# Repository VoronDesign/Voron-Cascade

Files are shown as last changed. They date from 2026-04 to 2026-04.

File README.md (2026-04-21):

# Voron Cascade
**[CLICK HERE TO DOWNLOAD](https://voron.zip/done/VC.zip)**

Image of Voron Cascade

The official release of the Voron Cascade desktop CNC milling machine.  You can find the BOM in the CAD directory or located at the [Voron Design](http://vorondesign.com/voron_cascade) website.

Voron Logo

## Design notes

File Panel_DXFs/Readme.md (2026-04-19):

\[sp-o\] for an opaque panel, structural / safety  
\[sp-c\] for a clear panel, structural / safety  
\[ep-o\] for an opaque panel used for an enclosure, non-structural  
\[ep-c\] for a clear panel used for an enclosure, non-structural

Frame bottom and gantry opaque panels should be 3mm (1/8") aluminum or steel.

Working enclosure clear panels should be 5mm (3/16") polycarbonate.

Frame or printed enclosure opaque panels should be 3mm (1/8") ABS.

Frame or printed enclosure clear panels should be 3mm (1/8") acrylic, preferably tinted ("smoked").

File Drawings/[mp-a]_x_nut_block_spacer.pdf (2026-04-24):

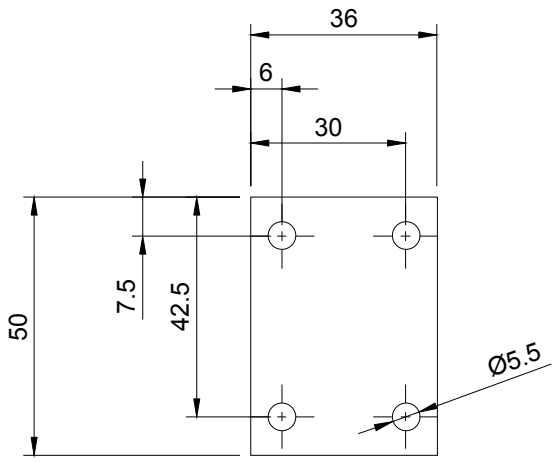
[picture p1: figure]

8.6

[mp-a]_x_nut_block_spacer

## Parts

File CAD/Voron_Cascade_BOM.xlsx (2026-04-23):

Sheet: BOM
Section / Item | Part Number | Quantity
Required Tools
600mm (24”) straight edge or level (ruler if no other choice) |  | 1
300mm (12”) metal machinist scale | Both inch and metric scales | 1
150mm (6”) calipers, preferably digital | 200mm / 8" as upgrade | 1
Dial indicator (metric or imperial) with mag base & arm | 25mm / 1" travel | 1
75mm (3”) machinist square, also 150mm (6”) if available. | Set of 4 | 1
123 blocks | with holes | 2
Step drill up to 1" / 25mm |  | 1
Main Frame
3030, 440mm, both ends tapped | HFSB6-3030-440-TPW | 2
3060, 410mm, both ends tapped | HFSB6-3060-410-TPW | 2
3060, 295mm, both ends tapped, counterbores | HFSB6-3060-295-TPW-Z8-YA15-YB45-YC140-YD170 | 2
3060, 410mm, both ends tapped, counterbores | HFSB6-3060-410-TPW-Z8-YA120-YB290 | 2
3060, 500mm, both ends tapped, counterbores | HFSB6-3060-500-TPW-Z8-XA120-XB150-YA15-YB485 | 1
3060, 500mm, both ends tapped, counterbores | HFSB6-3060-500-TPW-Z8-XA350-XB380-YA15-YB485 | 1
2020, 237mm, both ends tapped, wrench access holes | HFSB5-2020-237-TPW-AH50-BH75-CH205-DH230 | 2
Working Enclosure Frame
2020, 190mm, both ends tapped | HFSB5-2020-190-TPW | 2
2020, 265mm, both ends tapped | HFSB5-2020-265-TPW | 4
2020, 469mm, both ends tapped, wrench access holes | HFSB5-2020-469-TPW-LCP-RCP | 2
Frame Electronics Enclosure
2020, 380mm, both ends tapped | HFSB5-2020-380-TPW | 2
2020, 380mm, both ends tapped, wrench access holes | HFSB5-2020-380-TPW-AH20-BH90-CH190-DH360 | 2
2020, 290mm, both ends tapped | HFSB5-2020-290-TPW | 2
2020, 290mm, both ends tapped, wrench access hole | HFSB5-2020-290-TPW-AH20 | 2
2020, 160mm, both ends tapped, wrench access holes | HFSB5-2020-160-TPW-LCP-RCP | 4
Linear Rails
MGN15C LINEAR GUIDE RAIL, 200mm | MGN15, 200mm length, dual compact carriage | 2
MGN15H LINEAR GUIDE RAIL, 400mm | MGN15, 400mm length, dual carriage | 4
Motion Components
SFU1204 ball screw, 250mm | Assembly including BK10 and DSG12H (BF10 not used) | 1
SFU1204 ball screw, 400mm | Complete assembly including BK10, BF10, and DSG12H | 2
Motor drive pulley | HTD-3M 9mm width, 20 tooth, 5mm or 6.35mm bore (per motor) | 3
Ball screw drive pulley | HTD-3M 9mm width, 20 tooth, 8mm bore | 3
X,Y drive belts | HTD-3M 9mm width, closed loop, 189mm long | 2
Z drive belt | HTD-3M 9mm width, closed loop, 288mm long | 1
NEMA23 motor, up to 117mm length | LDO 57STH86-3004A | 3
Machined Parts (see other tab)
X Carriage Plate | [mp-a]_x_carriage_plate | 1
X Ballscrew Nut Spacer | [mp-a]_x_nut_block_spacer | 1
Y Ballscrew Front Mount | [mp-a]_y_ballscrew_mount_front | 1
Y Ballscrew Rear Mount | [mp-a]_y_ballscrew_mount_rear | 1
Y Carriage Spacer | [mp-a]_y_carriage_block | 2
Y Ballscrew Nut Spacer | [mp-a]_y_nut_block_spacer | 1
SELECT: Z Carriage Plate (50mm spindle mount) | [mp-a]_z_carriage_plate_M6_70x20 | 1
SELECT: Z Carriage Plate (65mm spindle mount) | [mp-a]_z_carriage_plate_M8_99x25 | 1
SELECT: Z Carriage Plate (80mm spindle mount) | [mp-a]_z_carriage_plate_M8_80x30 | 1
SELECT: Z Carriage Plate (blank, to be customized) | [mp-a]_z_carriage_plate_blank | 1
Panels (see other tab)
Opaque Frame Panels | Aluminum or Steel 3mm (1/8")
 | [sp-o]_frame_bottom_panel] (470x500) | 1
 | [sp-o]_gantry_back_panel (468x294) | 1
 | [sp-o]_gantry_front_brace (168x180) | 2
 | [sp-o]_gantry_side_brace_panel_left (354x135) | 1
 | [sp-o]_gantry_side_brace_panel_right (354x500) | 1
Clear Working Enclosure Panels | Polycarbonate 4.5mm or 5mm (3/16")
 | [sp-c]_working_enclosure_panel_back_top (468x35) | 1
 | [sp-c]_working_enclosure_panel_front_side (348x305) | 1
 | [sp-c]_working_enclosure_panel_front_top (468x210) | 1
 | [sp-c]_working_enclosure_panel_middle (468x305) | 2
Opaque Electronics Enclosure Panels | ABS / PC / nylon 3mm (1/8")
 | [ep-o]_frame_enclosure_panel_back (329x159) | 1
 | [ep-o]_frame_enclosure_panel_bottom (419x159) | 1
 | [ep-o]_frame_enclosure_panel_front (329x159) | 1
 | [ep-o]_frame_enclosure_panel_top (419x159) | 1
Smoked Electronics Enclosure Panels | Smoked Acrylic 3mm (1/8")
 | [ep-c]_frame_enclosure_panel_side (380x302) | 1
Work Table Options
Option 1: T-Slot table
T-Slot single sided extrusions | HFSQN4-15100-300 - cheaper option | 2
Option 2: Machined table
SMW 340x230 Grid Plate | Recommended upgrade - special order | 1
Spindle Options
Option 1: AC VFD (strongly preferred)
G-Penny 1.5kw 24k RPM ER16 spindle with H100 VFD | Package | 1
65mm Spindle clamp with 80x30 bolt pattern | G-Penny provided clamp does not fit | 1
Meanwell LRS-350-48 | Stepper motor power supply | 1
18 AWG (0.75mm^2), 3 core, braided shield, high flex VFD cable | Spindle cable is not provided | 2
Option 2: DC brushless (discouraged but possible)
500W Brushless ER16 (or ER11) Spindle | Commonly bought as package | 1
Meanwell SE-600-48 | <included in package> (dual purpose, spindle + stepper motors) | 1
Spindle Clamp | <included in package> | 1
WS55-220 | <included in package> | 1
Electronics
60mm Axial Fan, 24V |  | 1
DIN Rail, 350mm |  | 1
DIN Rail, 100mm |  | 1
Drag Chain 15x15 | 2-bolt end connectors | 1
E-Stop Button | 22mm through-hole, 1NO1NC | 1
PowerCON panel connector | Neutrik NAC3MPXXA | 1
PowerCON power cable | One end Neutrik NAC3FXXA, other end local mains connector | 1
24V, 30W power supply | Meanwell IRM-30-24ST | 1
5V, 30W power supply | Meanwell IRM-30-5ST | 1
Inductive end stop | PL-08N or equivalent | 3
TA35 rocker circuit breaker, 15A | Schurter TA35-CBDWF150C0 | 1
Mini contactor, DIN mounted, 120V or 240V coil voltage | Weg CWC025-00-30V18 (120V), CWC016-01-30V24 (230V) | 1
Sexbolt endstop PCB with included KW10 | Part of sexbolt endstop kit | 1
Daylight on a matchstick |  | 1
Flat button, M12 or M16 diameter, with nut | Preferably one each in red, green, and yellow (or white) | 3
KW10 microswitch | Used for door safety switch | 2
Wago 5-conductor | 220-415 | 7
3D probe - OPTIONAL | Must be normal open | 1
Above table tool setter - OPTIONAL |  | 1
Wire | 20awg PTFE, 2m | 1
 | 24awg PTFE, 4m | 1
 | 14awg PVC, 1m | 1
Controller Configuration
Option 1: Expatria FlexiHAL + external drivers
Expatria FlexiHAL control board |  | 1
DM542T stepper motor controller |  | 3
Option 2: BTT Scylla
BTT Scylla CNC control board | Motor drivers are included | 1
Local Management Computer
Raspberry Pi 4+ or better |  | 1
10.1" touchscreen with VESA 75 mount | 1280x800 minimum, HD (1920x1080) preferred | 1
USB-A to USB-C cable |  | 1
USB-C to bare wire power cable | Supplemental power for display | 1
Micro-HDMI to HDMI cable, 0.5m-1m long | Pi to touchscreen with no adapters | 1
180 angle USB-C adapter |  | 2
180 angle HDMI adapter |  | 1
USB-C keystone |  | 1
USB-C cable, 0.5m | internal cable for keystone | 1
Wireless mini-keyboard - OPTIONAL | Logitech K400 or similar | 1
Hardware
Rubber feet, 20mm diameter | GOM-04 | 6
M3 Threaded Insert, Voron spec |  | 38
M3 2020 T-Nut |  | 2
M3 3030 T-Nut |  | 60
M5 2020 T-Nut |  | 115
M5 3030 T-Nut |  | 43
M6 3030 T-Nut |  | 82
M3 Washer |  | 2
M4 Washer |  | 12
M5 Washer |  | 19
M6 Washer |  | 5
M8 Washer |  | 4
M3 Hex Nut |  | 3
M4 Hex Nut |  | 10
M5 Hex Nut |  | 21
M6 Hex Nut |  | 8
M8 Hex Nut |  | 1
M5x20 sexbolt / chicago bolt | Part of sexbolt endstop kit | 1
M2x10 Self-tapping Screw |  | 14
M3x8 FHCS |  | 7
M3x10 FHCS |  | 2
M3x10 BHCS |  | 8
M4x6 BHCS |  | 8
M4x14 BHCS |  | 18
M5x8 BHCS |  | 39
M5x10 BHCS |  | 79
M5x12 BHCS |  | 13
M5x16 BHCS |  | 34
M5x40 BHCS |  | 1
M6x10 BHCS |  | 85
M6x16 BHCS |  | 8
M8x10 BHCS |  | 5
M8x16 BHCS |  | 4
M3x8 SHCS |  | 9
M3x10 SHCS |  | 54
M3x12 SHCS |  | 65
M3x20 SHCS |  | 13
M3x25 SHCS |  | 6
M3x50 SHCS |  | 1
M4x6 SHCS | Part of sexbolt endstop kit | 1
M4x16 SHCS |  | 8
M5x10 SHCS |  | 9
M5x12 SHCS |  | 22
M5x16 SHCS |  | 9
M5x20 SHCS |  | 18
M5x25 SHCS |  | 6
M5x30 SHCS |  | 10
M5x60 SHCS |  | 2
M6x35 SHCS |  | 11
M6x40 SHCS |  | 6
M6x65 SHCS | Optional, For 50mm spindle mount | 4
M8x40 SHCS |  | 20
M8x70 SHCS |  | 8
M8x90 SHCS | Optional, For 80mm spindle mount | 4
M6x100 threaded rod |  | 1
Precision shim tape, 0.1mm (0.004”) thick, <10mm wide |  | 1
Accordion cover 15mmx300mm | Fabric (rubber infused) is preferred over plastic for flexibility. | 2
Loctite 242 or equivalent |  | 1
1/4”x4” hardened steel dowel |  | 1
2mm x 100mm (4") zip ties |  | 50
2020 extrusion slot cover, 1m section |  | 3
3030 extrusion slot cover, 1m section |  | 12
MGN12 rail plugs | Used for X and Z rails only | 50
Tools for drilling extrusion bed | Only needed if buying raw extrusion bed parts
1/8" / 3mm drill bit |  | 1
3/16 / 5mm drill bit |  | 1
Tools for drilling and preparing extrusions and panels | Only needed if buying raw extrusions and panels
9/64" / 3.5mm drill bit |  | 1
7/32" / 5.5mm drill bit |  | 1
21/64" / 8.5mm drill bit |  | 1
M8 counterbore tool |  | 1
9/16" endmill with 1/2" shank | Only if M8 counterbore is unavailable
M3 tap |  | 1
M5 tap |  | 1
M8 tap |  | 1
Tap handle (if not already owned) |  | 1

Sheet: Printed & Machined Parts
Printed Parts
Category | Name | Count | Color | Material | Notes
Tools and Guides - Frame Drilling | [pp-p]_drill_jig_frame_base_corners | 1 | N/A | PLA | Only needed if self drilling frame | [pp-p] for printed part, primary color
 | [pp-p]_drill_jig_frame_base_gantry | 1 | N/A | PLA | Only needed if self drilling frame | [pp-s] for printed part, secondary color
 | [pp-p]_drill_jig_frame_base_rails | 1 | N/A | PLA | Only needed if self drilling frame | [pp-c] for printed part, clear PETG
 | [pp-p]_drill_jig_gantry_frame_left | 1 | N/A | PLA | Only needed if self drilling frame | [mp-a] for a machined part, aluminum
 | [pp-p]_drill_jig_gantry_frame_right | 1 | N/A | PLA | Only needed if self drilling frame | [sp-o] for an opaque panel, structural / safety
 |  |  |  |  |  | [sp-c] for a clear panel, structural / safety
Tools and Guides - Panel Drilling | [pp-p]_drill_template_60mm_fan | 1 | N/A | PLA | Only needed if self cutting panels | [ep-o] for an opaque panel used for an enclosure, non-structural
 | [pp-p]_drill_template_60mm_fan_with_keystones | 1 | N/A | PLA | Only needed if self cutting panels | [ep-c] for a clear panel used for an enclosure, non-structural
 | [pp-p]_drill_template_display_mount | 1 | N/A | PLA | Only needed if self cutting panels
 | [pp-p]_drill_template_power_inlet | 1 | N/A | PLA | Only needed if self cutting panels
Tools and Guides - Assembly & Alignment | [pp-p]_1204_screw_clamp_A | 1 | N/A | PLA
 | [pp-p]_1204_screw_clamp_B | 1 | N/A | PLA
 | [pp-p]_alignment_guide_2020_mgn15 | 2 | N/A | PLA
 | [pp-p]_alignment_guide_3030_mgn15 | 2 | N/A | PLA
 | [pp-p]_alignment_guide_3060_mgn15 | 2 | N/A | PLA
 | [pp-p]_alignment_tool_x_axis | 1 | N/A | PLA
 | [pp-p]_alignment_tool_y_axis | 1 | N/A | PLA
 | [pp-p]_alignment_tool_y_drive | 1 | N/A | PLA
 | [pp-p]_ballscrew_1204_maint_tool | 1 | N/A | PLA
 | [pp-p]_setup_tool_z | 1 | N/A | PLA
 | [pp-p]_tramming_bar | 1 | N/A | PLA
Core Frame and Drive | [pp-s]_x_endstop_mount_long_body | 1 | accent | ABS | Choose 1 of 4 (no 3d probe, long sensor)
 | [pp-s]_x_endstop_mount_short_body | 1 | accent | ABS | Choose 1 of 4 (no 3d probe, short sensor)
 | [pp-s]_x_endstop_probe_mount_long_body | 1 | accent | ABS | Choose 1 of 4 (3d probe, long sensor)
 | [pp-s]_x_endstop_probe_mount_short_body | 1 | accent | ABS | Choose 1 of 4 (3d probe, short sensor)
 | [pp-s]_x_endstop_trigger_mount | 1 | accent | ABS
 | [pp-s]_z_carriage_cover_air_mount | 1 | accent | ABS | Choose 1 of 2
 | [pp-s]_z_carriage_cover_blank | 1 | accent | ABS | Choose 1 of 2
 | [pp-s]_z_drive_belt_guard | 1 | accent | ABS
 | [pp-s]_z_drive_mount | 1 | accent | ABS
 | [pp-s]_z_drive_mount_cover | 1 | accent | ABS
 | [pp-s]_z_endstop_clamp | 1 | accent | ABS
 | [pp-p]_3030_m6_nut_carrier | 1 | primary | ABS
 | [pp-p]_frame_cable_routing_cover | 1 | primary | ABS
 | [pp-p]_frame_endstop_cable_guide | 1 | primary | ABS
 | [pp-p]_gantry_chain_mount | 1 | primary | ABS
 | [pp-p]_rail_stop_20mm | 2 | primary | ABS
 | [pp-p]_sexbolt_debris_shield_extrusion | 1 | primary | ABS | Choose 1 of 2
 | [pp-p]_sexbolt_debris_shield_grid | 1 | primary | ABS | Choose 1 of 2
 | [pp-p]_tool_setter_cable_guide_OPTIONAL | 1 | primary | ABS | Only if using above table tool setter
 | [pp-p]_tool_setter_under_mount_extrusion | 1 | primary | ABS | Choose 1 of 2, only for under table tool setter
 | [pp-p]_tool_setter_under_mount_grid | 1 | primary | ABS | Choose 1 of 2, only for under table tool setter
 | [pp-p]_x_ballscrew_block_mount | 1 | primary | ABS
 | [pp-p]_x_motor_mount | 1 | primary | ABS
 | [pp-p]_x_spacer_washer_guide | 1 | primary | ABS
 | [pp-p]_y_endstop_mount_long_body | 1 | primary | ABS | Choose 1 of 2
 | [pp-p]_y_endstop_mount_short_body | 1 | primary | ABS | Choose 1 of 2
 | [pp-p]_y_motor_mount | 1 | primary | ABS
 | [pp-p]_y_motor_tension_block | 1 | primary | ABS
Electrical | [pp-s]_air_inlet_cover_hex | 1 | accent | ABS
 | [pp-s]_air_inlet_cover_mount_ring | 1 | accent | ABS
 | [pp-s]_fan_cover_keystone_hex | 1 | accent | ABS
 | [pp-s]_fan_cover_mount_plate | 1 | accent | ABS
 | [pp-s]_keystone_blank | 2 | accent | ABS
 | [pp-c]_daylight_cover | 1 | clear | PETG
 | [pp-p]_DIN Clips | 1 | primary | ABS
 | [pp-p]_IRM-30-XXST_din_mount | 2 | primary | ABS
 | [pp-p]_WAGO_221-415_3x5_2020mount | 1 | primary | ABS
 | [pp-p]_WAGO_221-415_2x5-2020mount | 2 | primary | ABS
 | [pp-p]_cable_mount_20mm | 8 | primary | ABS
 | [pp-p]_flexihal_DIN_mount_pair | 1 | primary | ABS | Only if using FlexiHAL controller
 | [pp-p]_scylla_DIN_mount_pair | 1 | primary | ABS | Only if using Scylla controller
 | [pp-p]_lrs_350_saddle_mount | 2 | primary | ABS | Only if using LRS 350 48V power supply
 | [pp-p]_se_600_mount_A | 1 | primary | ABS | Only if using SE600 48V power supply
 | [pp-p]_se_600_mount_B | 1 | primary | ABS | Only if using SE600 48V power supply
 | [pp-p]_pi_mount_2020 | 1 | primary | ABS
 | [pp-p]_power_inlet_panel_mount_ring | 1 | primary | ABS
 | [pp-p]_power_inlet_panel_powercon | 1 | primary | ABS
Workspace Enclosure | [pp-s]_3030_enclosure_panel_clip | 6 | accent | ABS
 | [pp-s]_3060_end_cap_enclosure_panel_clip | 4 | accent | ABS
 | [pp-p]_enclosure_handle | 3 | primary | ABS
 | [pp-p]_working_enclosure_frame_mount_front | 1 | primary | ABS
 | [pp-p]_working_enclosure_rear_mount_left | 1 | primary | ABS
 | [pp-p]_working_enclosure_rear_mount_right | 1 | primary | ABS
Frame Enclosure | [pp-s]_frame_enclosure_corner_cap_foot | 2 | accent | ABS
 | [pp-s]_frame_enclosure_corner_cap_plain | 2 | accent | ABS
 | [pp-s]_panel_frame_hook_A | 1 | accent | ABS
 | [pp-s]_panel_frame_hook_B | 1 | accent | ABS
 | [pp-s]_panel_latch_arm_A | 1 | accent | ABS
 | [pp-s]_panel_latch_arm_B | 1 | accent | ABS
 | [pp-s]_panel_latch_corner_mount_A | 1 | accent | ABS
 | [pp-s]_panel_latch_corner_mount_B | 1 | accent | ABS
 | [pp-p]_cable_protection_fitting | 1 | primary | ABS
 | [pp-p]_cable_protection_nut | 1 | primary | ABS
 | [pp-p]_display_mount_landscape_front | 1 | primary | ABS | If using display in landscape orientation
 | [pp-p]_display_mount_landscape_rear | 1 | primary | ABS | If using display in landscape orientation
 | [pp-p]_display_mount_portrait_front | 1 | primary | ABS | If using display in portrait orientation
 | [pp-p]_display_mount_portrait_rear | 1 | primary | ABS | If using display in portrait orientation
Trim | [pp-s]_3060_end_cap_logo | 1 | accent | ABS
 | [pp-p]_accordion_cover_mount_A | 2 | primary | ABS
 | [pp-p]_accordion_cover_mount_B | 2 | primary | ABS
 | [pp-p]_debris_shield_back_left | 1 | primary | ABS
 | [pp-p]_debris_shield_back_right | 1 | primary | ABS
 | [pp-p]_debris_shield_front_left | 1 | primary | ABS
 | [pp-p]_debris_shield_front_right | 1 | primary | ABS
 | [pp-p]_gantry_front_brace_cover | 2 | primary | ABS
 | [pp-p]_x_drive_debris_cover_left | 1 | primary | ABS
 | [pp-p]_x_drive_debris_cover_right | 1 | primary | ABS
Machined Parts
Core Frame and Drive | [mp-a]_x_carriage_plate | 1 | N/A | aluminum
 | [mp-a]_x_nut_block_spacer | 1 | N/A | aluminum
 | [mp-a]_y_ballscrew_mount_front | 1 | N/A | aluminum
 | [mp-a]_y_ballscrew_mount_rear | 1 | N/A | aluminum
 | [mp-a]_y_carriage_block | 2 | N/A | aluminum
 | [mp-a]_y_nut_block_spacer | 1 | N/A | aluminum
 | [mp-a]_z_carriage_plate_M6_70x20 | 1 | N/A | aluminum | choose one based on spindle mount
 | [mp-a]_z_carriage_plate_M8_99x25 | 1 | N/A | aluminum | choose one based on spindle mount
 | [mp-a]_z_carriage_plate_M8_80x30 | 1 | N/A | aluminum | choose one based on spindle mount
 | [mp-a]_z_carriage_plate_blank | 1 | N/A | aluminum | choose one based on spindle mount
Panels - Laser or by hand
Core Frame and Drive | [sp-o]_frame_bottom_panel | 1 |  | steel / aluminum | 3mm
 | [sp-o]_gantry_back_panel | 1 |  | steel / aluminum | 3mm
 | [sp-o]_gantry_front_brace | 2 |  | steel / aluminum | 3mm
 | [sp-o]_gantry_side_brace_panel_left | 1 |  | steel / aluminum | 3mm
 | [sp-o]_gantry_side_brace_panel_right | 1 |  | steel / aluminum | 3mm
Workspace Enclosure | [sp-c]_working_enclosure_panel_back_top | 1 |  | polycarbonate | 5mm
 | [sp-c]_working_enclosure_panel_front_side | 1 |  | polycarbonate | 5mm
 | [sp-c]_working_enclosure_panel_front_top | 1 |  | polycarbonate | 5mm
 | [sp-c]_working_enclosure_panel_middle | 2 |  | polycarbonate | 5mm
Frame Enclosure | [ep-c]_frame_enclosure_panel_side | 1 |  | acrylic or PC | 3mm, smoked or clear
(Must pick frame or printed) | [ep-o]_frame_enclosure_panel_back | 1 |  | ABS or PC | 3mm
 | [ep-o]_frame_enclosure_panel_bottom | 1 |  | ABS or PC | 3mm
 | [ep-o]_frame_enclosure_panel_front | 1 |  | ABS or PC | 3mm
 | [ep-o]_frame_enclosure_panel_top | 1 |  | ABS or PC | 3mm

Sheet: Recommended Tools
Recommended additionalmeasuring and cutting tools for those new to machining
For things that measure and things that cut, you get what you pay for!
Measuring & Setup Tools | Notes | Quantity | Link
25mm or 1" micrometer |  | 1
Scribe with carbide tip |  | 1
Feeler gauge set |  | 1 | https://www.aliexpress.com/item/1005005899956007.html
Edge finder, 1/4" or 3/8" shank |  | 1
Tape measure |  | 1
Combination wrench set | Both inch and metric | 1
Hex key set | Both inch and metric | 1
Deadblow hammer |  | 1
Deburring tool set |  | 1
File set |  | 1
Machinist reference |  | 1
Workholding and Cutting
Low profile vise |  | 1
1/8" flat bottom single flute endmills, carbide and HSS | expect to break them | 4
1/8" flat bottom 2-flute endmills, HSS |  | 2
1/8" ball end endmills |  | 2

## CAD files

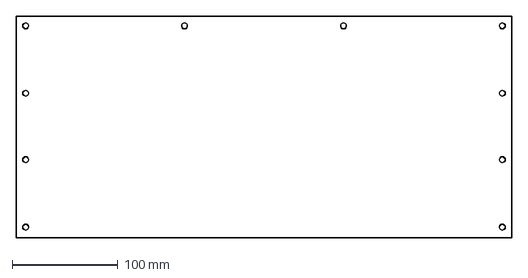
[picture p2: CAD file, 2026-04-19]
Panel_DXFs/[sp-c]_working_enclosure_panel_front_top.dxf
468.0 x 209.0 mm

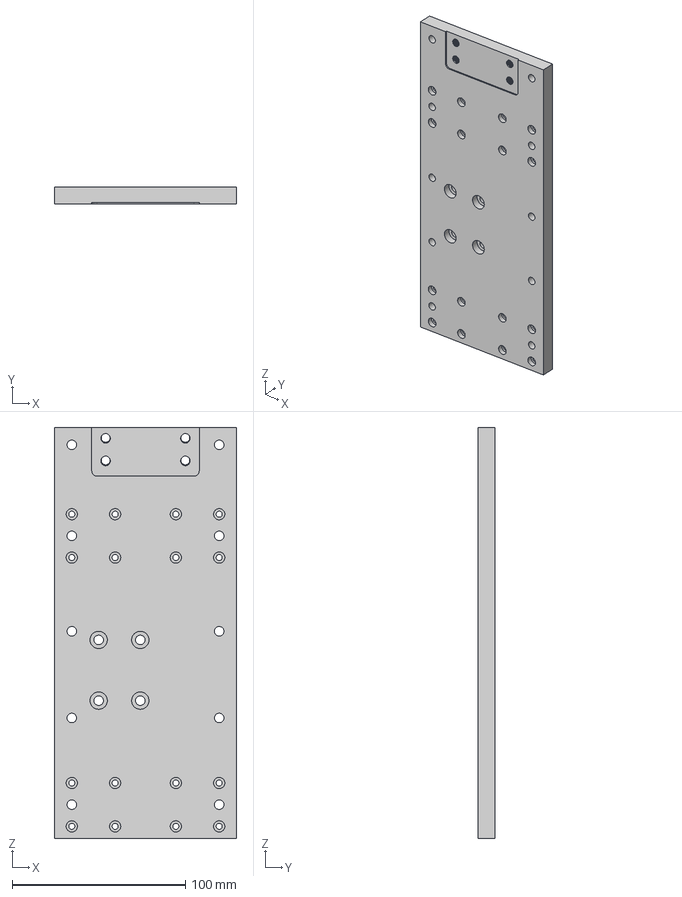
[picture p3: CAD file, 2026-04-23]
STEPs/[mp-a]_x_carriage_plate.step
105.0 x 10.0 x 237.0 mm

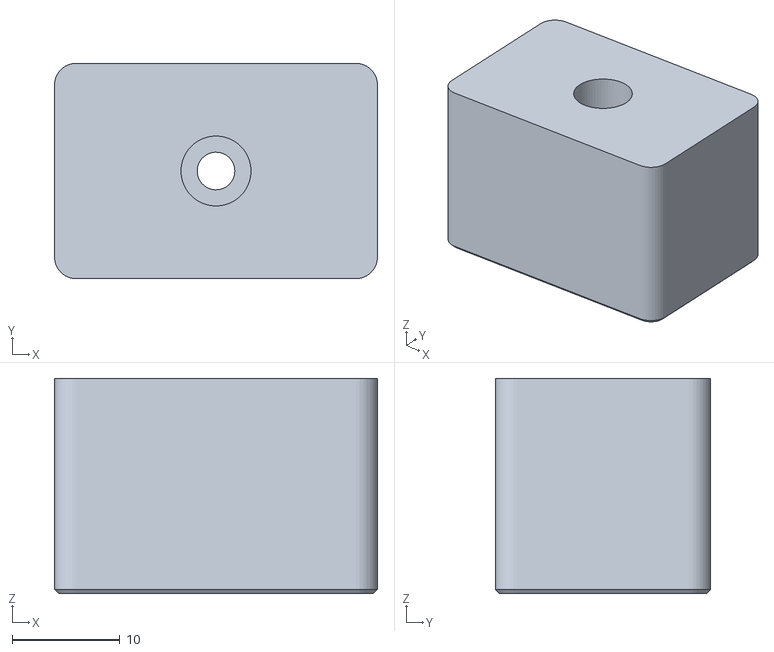
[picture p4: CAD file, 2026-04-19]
STLs/Base/[pp-p]_rail_stop_20mm_x2.stl
30.0 x 20.0 x 20.0

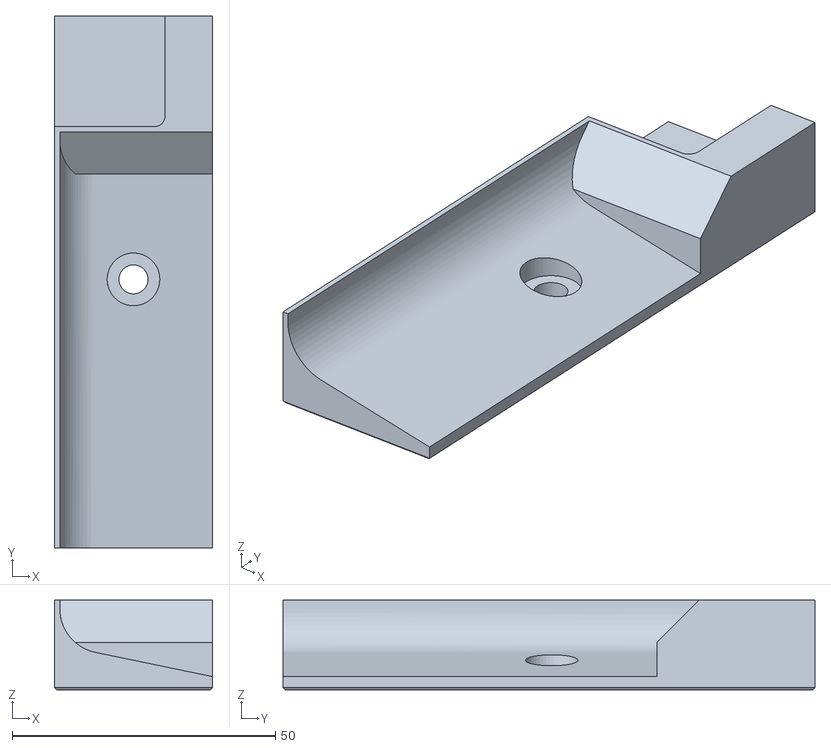
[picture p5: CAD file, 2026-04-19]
STLs/Base/Debris Shield/[pp-p]_debris_shield_back_left.stl
30.0 x 101.0 x 17.0

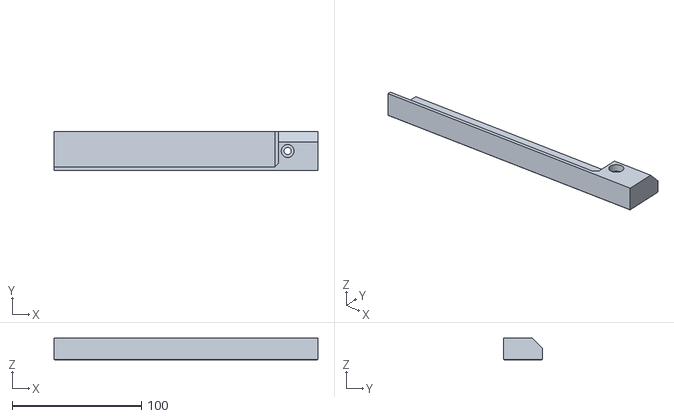
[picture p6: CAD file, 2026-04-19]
STLs/Base/Debris Shield/Accordion Cover Mount/[pp-p]_accordion_cover_mount_B_x2.stl
204.5 x 30.0 x 17.0

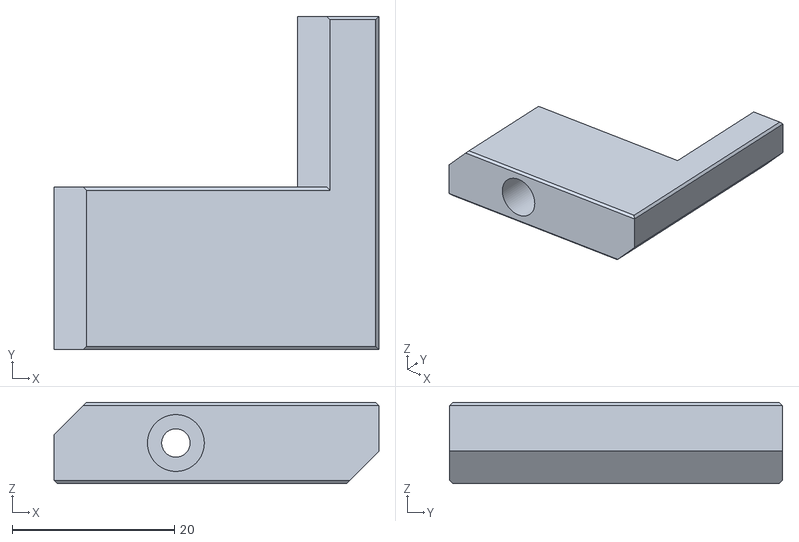
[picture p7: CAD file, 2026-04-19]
STLs/Base/Endstop Cable Guide/[pp-p]_frame_endstop_cable_guide.stl
40.0 x 41.0 x 10.0

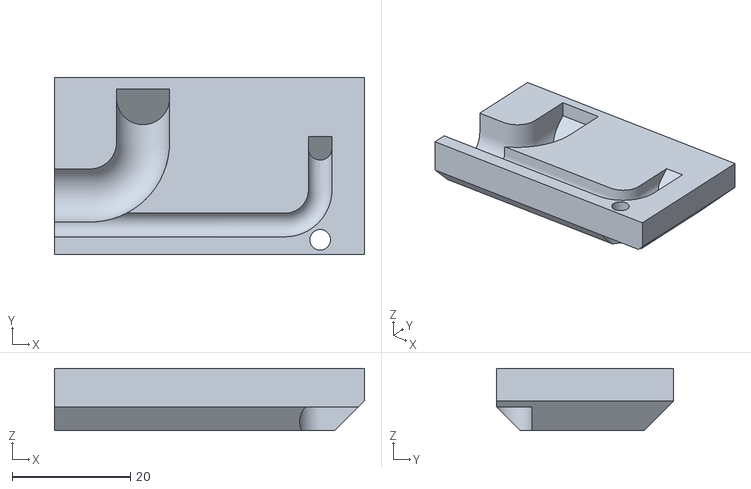
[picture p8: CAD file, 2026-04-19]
STLs/Base/Frame Cable Routing/[pp-p]_frame_cable_routing_cover.stl
52.5 x 30.0 x 10.5

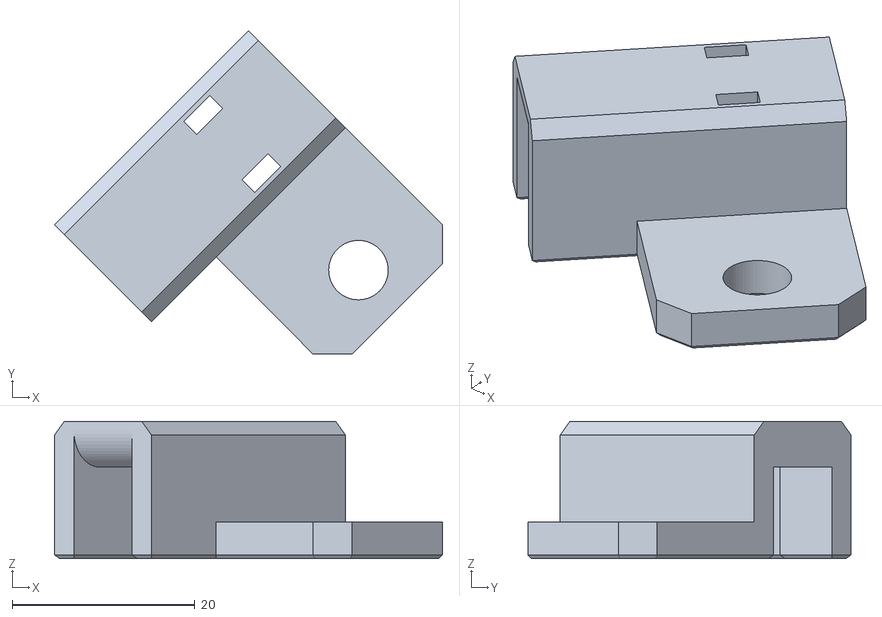
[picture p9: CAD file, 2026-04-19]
STLs/Base/Worktable/Tool Setter (Above) OPTIONAL/[pp-p]_tool_setter_cable_guide_OPTIONAL.stl
42.4 x 35.4 x 15.0

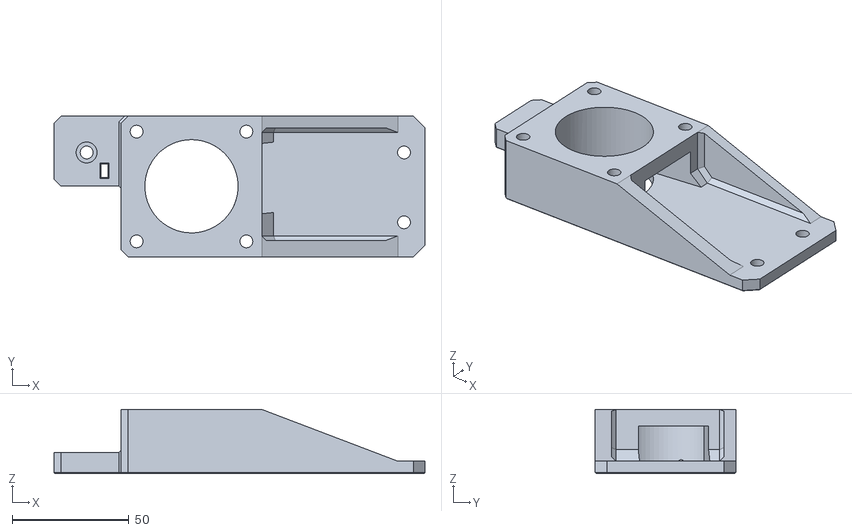
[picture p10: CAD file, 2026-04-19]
STLs/Base/Y Drive Assembly/Y Motor Mount/[pp-p]_y_motor_mount.stl
159.2 x 60.4 x 27.5

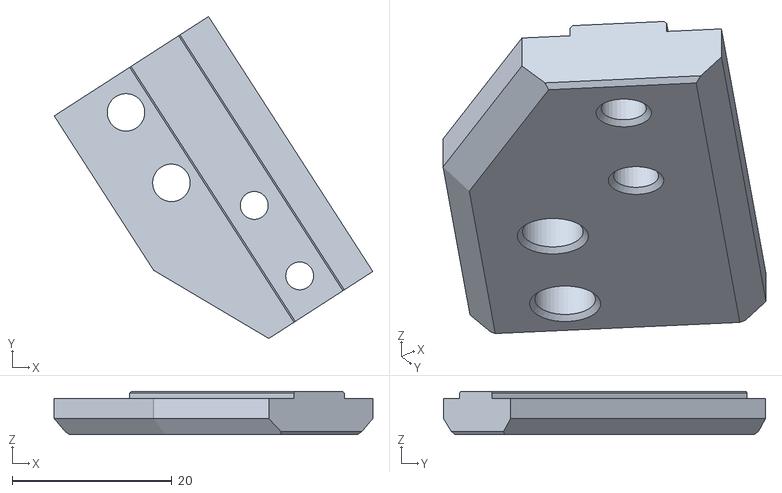
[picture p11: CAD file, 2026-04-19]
STLs/Base/Y Endstop/[pp-p]_y_endstop_mount_short_body.stl
39.9 x 40.3 x 5.40

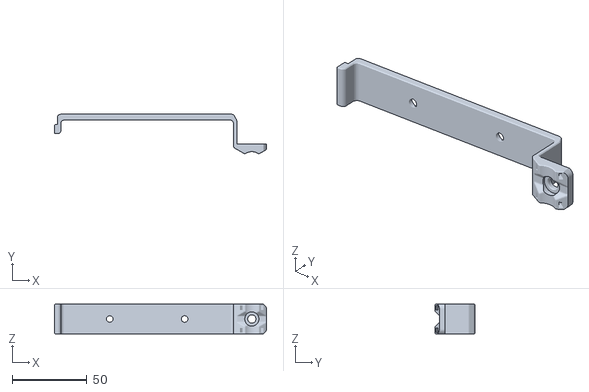
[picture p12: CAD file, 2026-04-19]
STLs/Electronics/AC Spindle/[pp-p]_lrs_350_saddle_mount_x2.stl
141.6 x 26.4 x 20.0

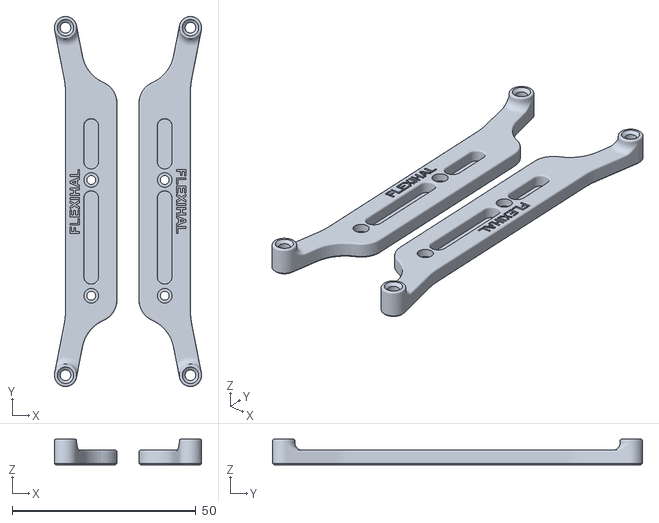
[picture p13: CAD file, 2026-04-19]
STLs/Electronics/Controller/[pp-p]_flexihal_DIN_mount_pair.stl
40.1 x 100.7 x 7.00

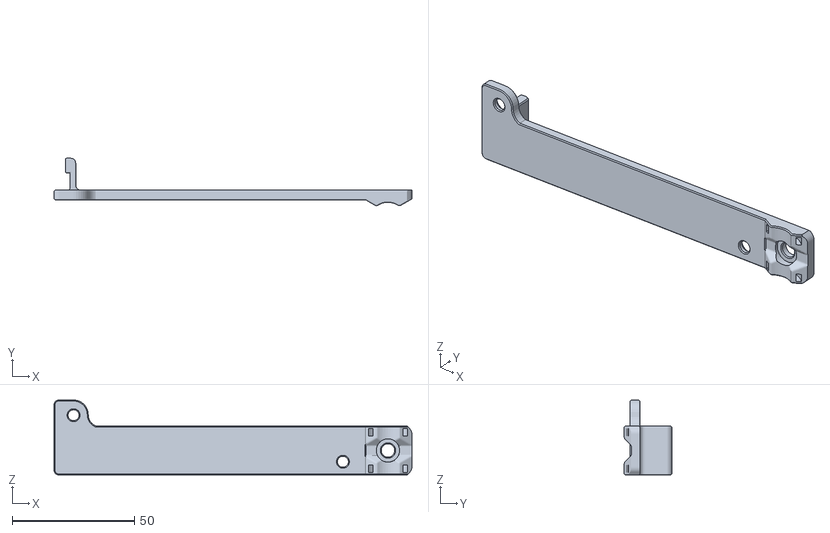
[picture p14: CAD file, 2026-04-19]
STLs/Electronics/DC 48V Spindle OPTIONAL/[pp-p]_se_600_mount_B.stl
146.2 x 19.4 x 30.6

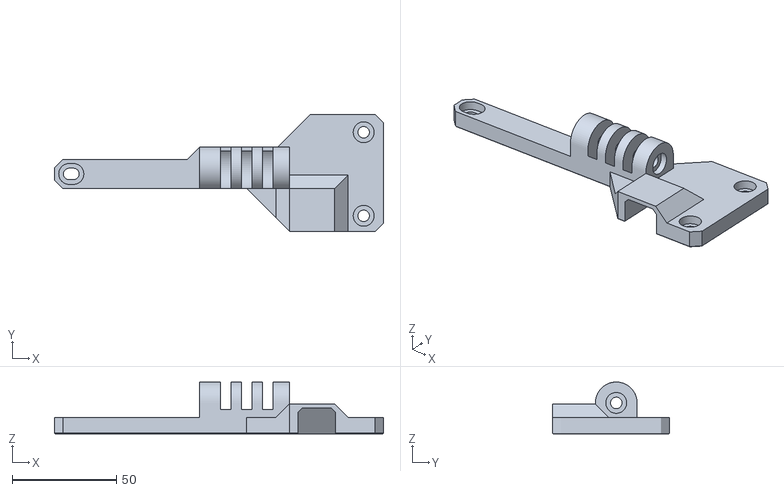
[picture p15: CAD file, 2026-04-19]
STLs/Electronics/Display Mount/[pp-p]_display_mount_portrait_rear.stl
157.5 x 56.0 x 24.9

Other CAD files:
STLs/Electronics/Electronics Hardware/[pp-s]_air_inlet_cover_mount_ring.stl
STLs/Electronics/Electronics Power/[pp-s]_keystone_blank_x2.stl
STLs/Electronics/Frame Enclosure/[pp-p]_cable_mount_20mm_x8.stl
STLs/Electronics/Frame Enclosure/Frame Enclosure Latch Corner/[pp-s]_panel_frame_hook_B.stl
Panel_DXFs/[ep-c]_frame_enclosure_panel_side.dxf
Panel_DXFs/[ep-o]_frame_enclosure_panel_back.dxf
Panel_DXFs/[ep-o]_frame_enclosure_panel_bottom.dxf
Panel_DXFs/[ep-o]_frame_enclosure_panel_front.dxf
Panel_DXFs/[ep-o]_frame_enclosure_panel_top.dxf
Panel_DXFs/[sp-c]_working_enclosure_panel_back_top.dxf
Panel_DXFs/[sp-c]_working_enclosure_panel_front_side.dxf
Panel_DXFs/[sp-c]_working_enclosure_panel_middle_x2.dxf
Panel_DXFs/[sp-o]_frame_bottom_panel.dxf
Panel_DXFs/[sp-o]_gantry_back_panel.dxf
Panel_DXFs/[sp-o]_gantry_front_brace_x2.dxf
Panel_DXFs/[sp-o]_gantry_side_brace_panel_left.dxf
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

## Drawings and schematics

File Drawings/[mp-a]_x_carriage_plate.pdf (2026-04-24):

187

237

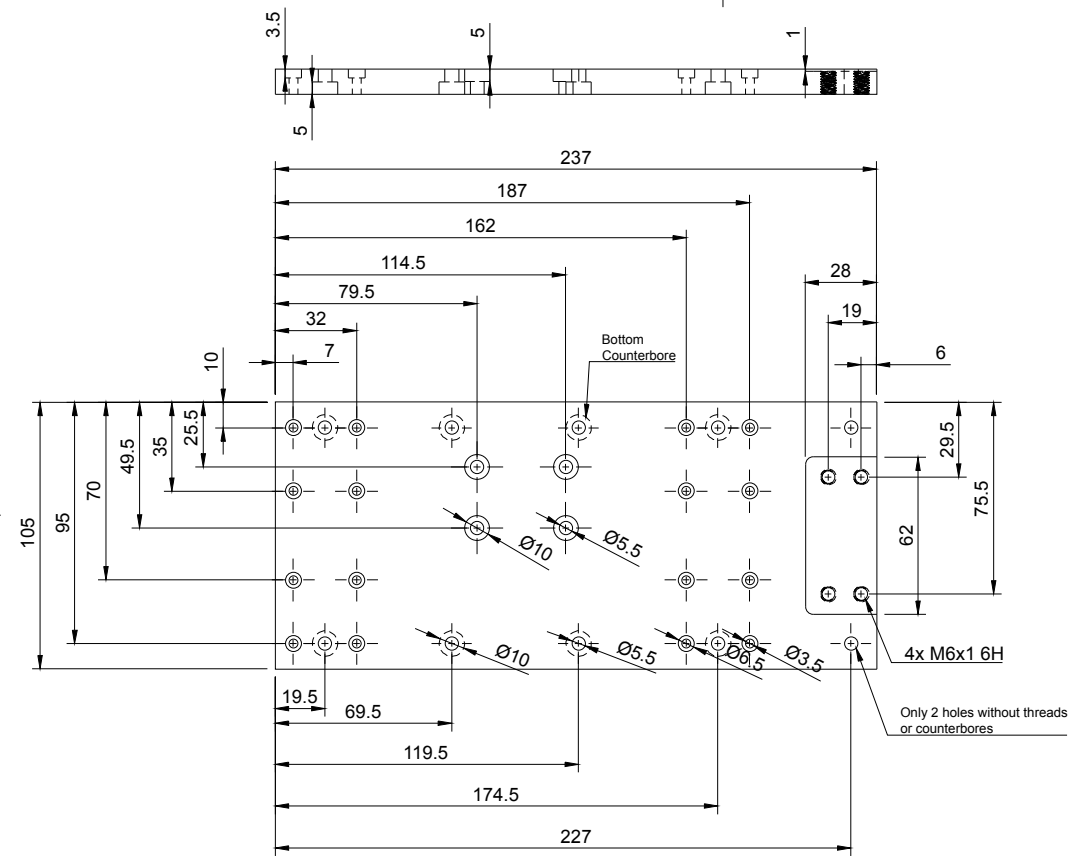
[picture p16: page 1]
Bottom Counterbore

Only 2 holes without threads
or counterbores

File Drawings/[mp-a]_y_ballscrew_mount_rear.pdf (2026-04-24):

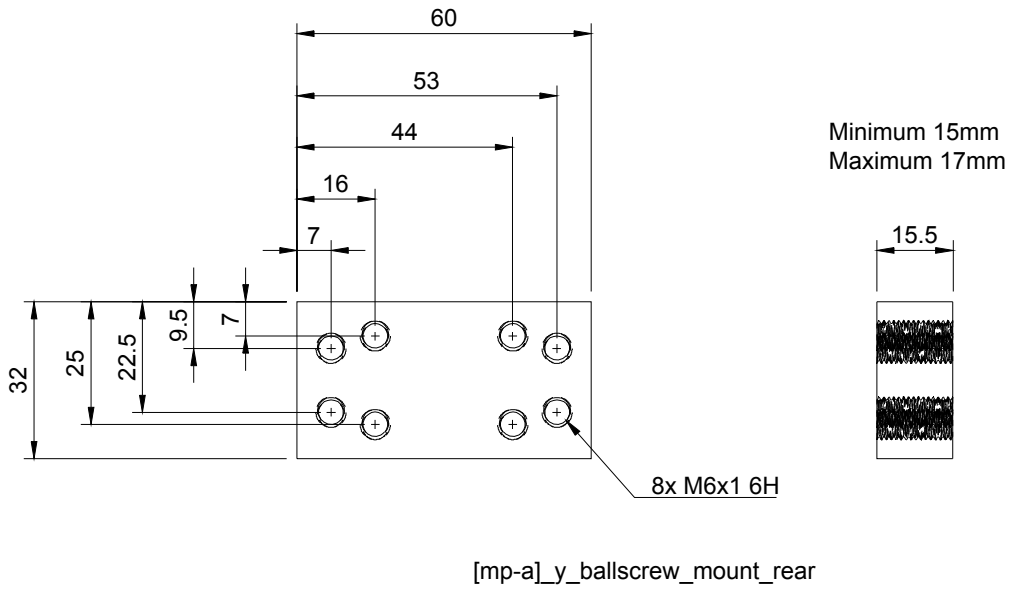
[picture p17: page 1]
Minimum 15mm Maximum 17mm; [mp-a]_y_ballscrew_mount_rear

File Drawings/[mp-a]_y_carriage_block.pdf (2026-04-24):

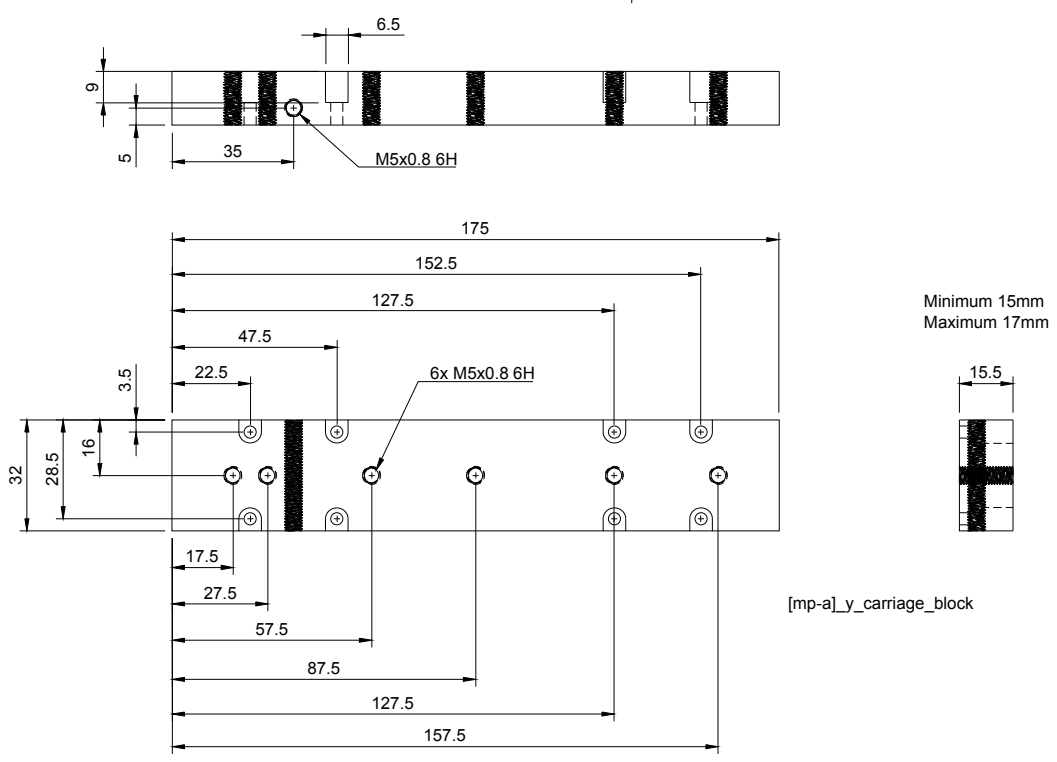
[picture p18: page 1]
Minimum 15mm Maximum 17mm; [mp-a]_y_carriage_block

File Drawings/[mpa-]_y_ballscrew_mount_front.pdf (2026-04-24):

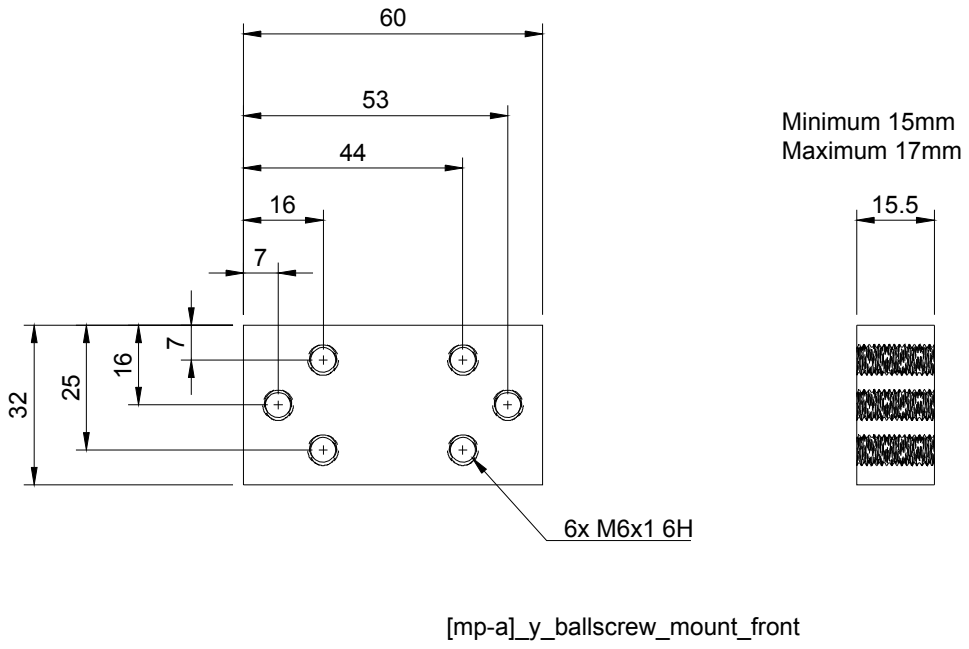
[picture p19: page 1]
Minimum 15mm Maximum 17mm; [mp-a]_y_ballscrew_mount_front

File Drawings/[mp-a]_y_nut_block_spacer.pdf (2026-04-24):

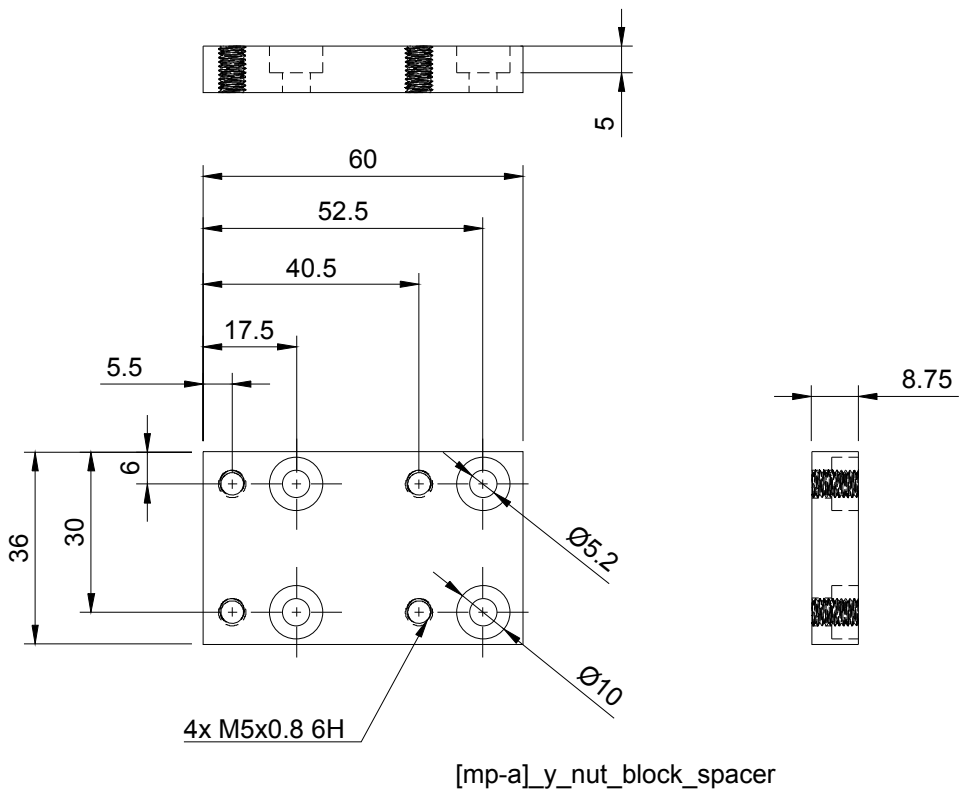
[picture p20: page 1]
[mp-a]_y_nut_block_spacer

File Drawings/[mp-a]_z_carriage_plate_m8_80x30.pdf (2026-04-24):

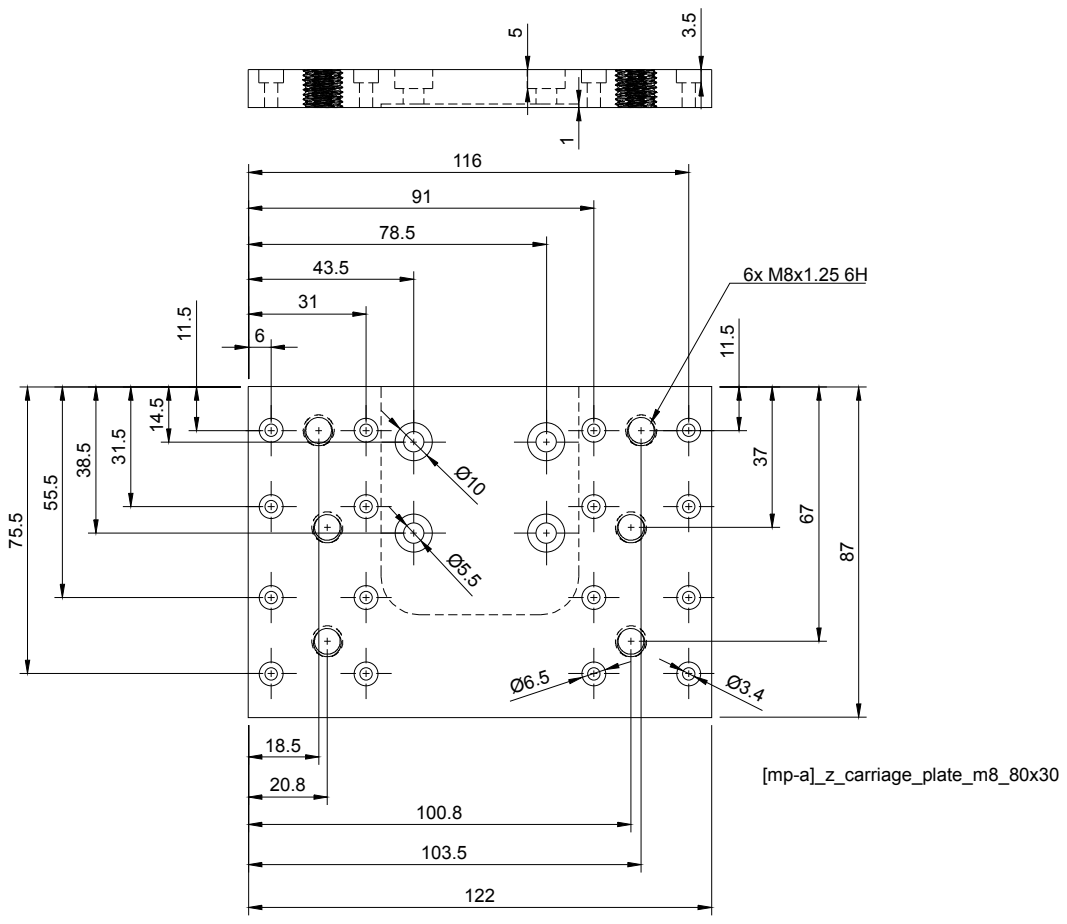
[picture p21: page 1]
Dept.; Technical reference; Created by; Approved by; Document type; Document status; Title; DWG No.; Cascade; Doug Bell; [mp-a]_z_carriage_plate_m8_80x30

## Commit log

2026-04-19 Fixed typo
    [[ep-c]_frame_enclosure_panel_side.dxf, [ep-o]_frame_enclosure_panel_back.dxf, [ep-o]_frame_enclosure_panel_bottom.dxf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]
2026-04-19 Added BOM file
    [Voron_Cascade_BOM.xlsx]
2026-04-19 BOM clarification
    [Voron_Cascade_BOM.xlsx]
2026-04-22 Updated BOM xls
    [Voron_Cascade_BOM.xlsx]
2026-04-23 Fixed issue with one extrusion below the minimum Misumi hole spacing
    [Voron_Cascade_BOM.xlsx, [mp-a]_x_carriage_plate.step]
